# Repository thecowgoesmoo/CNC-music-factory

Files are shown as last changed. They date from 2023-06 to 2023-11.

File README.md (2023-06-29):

# CNC-music-factory
This is my set of upgrades to a baseline 3018 CNC to support machining of wood for guitar necks, organ pipes, and other noisy bits.

The resulting machine has nearly 5x the cutting volume (300mm x 775mm x 50mm instead of the stock volume of 300mm x 180mm x 45mm) and 10 times the power (The spindle has been upgraded from the stock 75W one to a 750W Bosch Colt router).

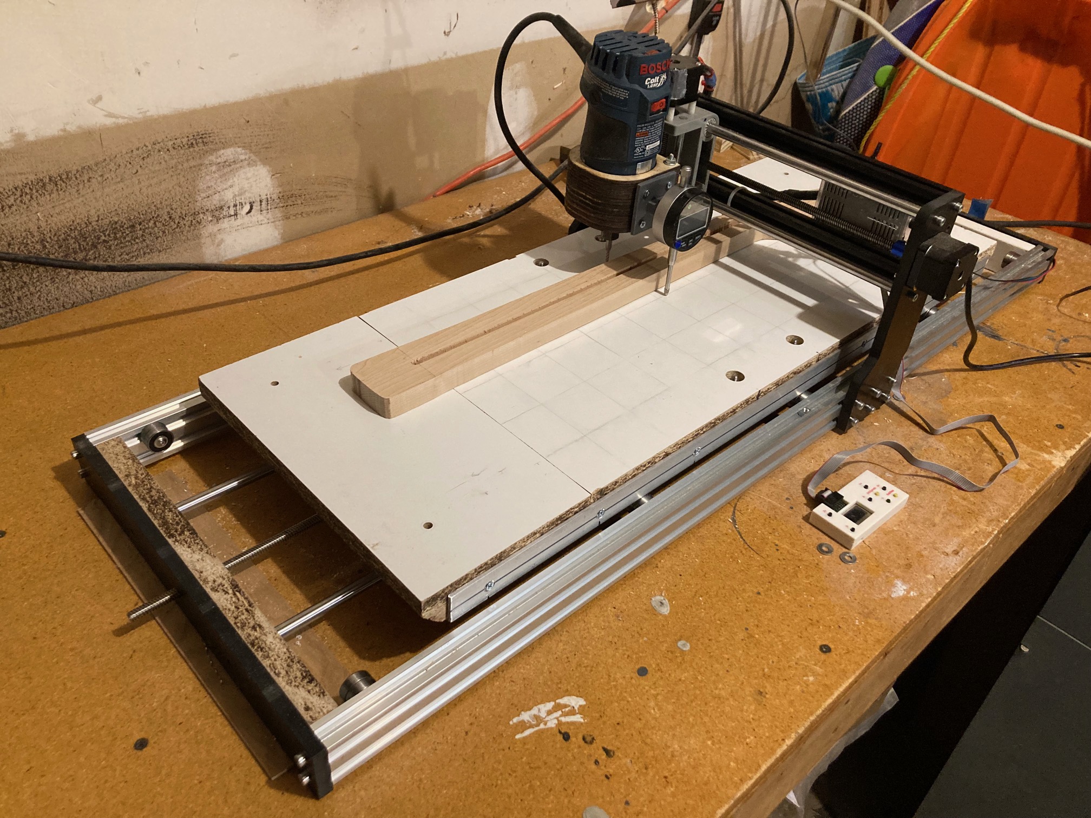
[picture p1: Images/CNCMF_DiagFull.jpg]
Overview image


## Overview
Playing music and making/modifying musical instruments has been a lifelong hobby of mine.  Electronic instruments have long been more accessible to DIY hobbyists given the increasing availability of custom printed circuit boards and the relatively low cost of basic electronic assembly tools.  3D printing and affordable hobbyist CNC machines have made construction of custom acoustic and electromechanical instruments more accessible than ever before.  

3D printing has been exciting, but available materials are not ideal for some acoustic applications (relatively high density and low stiffness compared to wood, for instance).  Laser cutting is a strong complementary technology, and K40 lasers have also achieved a <$500 USD price point, but these are largely limited to 2 dimensional cuts.  

A Genmitsu 3018 CNC has opened up new materials and geometries to me and had an initial price that was within my reach (<$200 USD).  The CAD and CAM learning curves proved considerably steeper than the SW tools for 3D printing, where large databases of free designs are readily available online and slicing SW is now relatively mature, general, and user-friendly.  And as I learned to use the 3018, its actual power, geometry, and accuracy proved to be quite constraining.  In particular, I was interested in being able to machine guitar necks from wood in less than a day of machining and without workpiece tiling.  As with lasers, there is a considerable price jump from the entry-level machines (~$200USD) to mid-level hobby machines (>$1000USD). 

My solution has been incremental upgrades, first to improve accuracy, then power, then machining volume.  The resulting machine appears to fill a capability and price point gap in the current commercial offerings (~$250USD beyond the baseline 3018 cost for 10x spindle power and a 1 meter y axis), so I've decided to share my set of upgrades for others to use if they please.  

## Assembly
1. Start with assembled and tested Genmitsu 3018 CNC
- a. Assuming Candle for pushing g code
- b. Assuming Fusion 360 for CAM
2. Build waste board
- a. Screw 1"x2" lumber to sides of melamine cut to dimensions
- b. Drill and countersink for mounting to aluminum plate
- c. Drill and mount aluminum side rails
- d. Bevel ends
3. Install lengthened Y axis:
- a. Remove existing Y axis v rail, linear bearing rails, and lead screw
- b. Install longer Y axis v rail, linear bearing rails (on plywood ends), and lead screw
- c. Mount extended waste board
- d. Install extension cable for stepper motor
4. Build new spindle carriage
- a. Cut profiles from plywood with laser
- b. Print assembly guides
- c. Glue, stack, and bolt with guides in place
- d. After drying, install antibacklash nut and linear bearings
- e. Mount new carriage on lead screw and linear rails and couple to stepper motor
5. Final bits
- a. Install 608 rollers under bed
- b. Print and install guide rollers for side/top
- c. Install carriage and check full range of travel for all axes
- d. Print and install meter mount
- e. Update GRBL setting for Y axis scaling
- f. Check bed leveling with meter
- g. Attach pen and draw shapes CW and CCW to check for backlash
6. First cut
- a. Run circle diamond square test

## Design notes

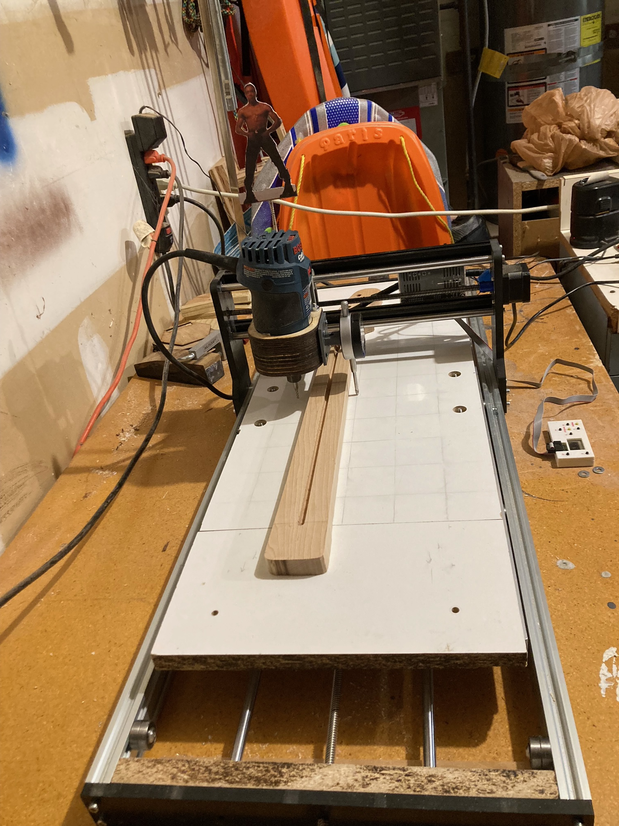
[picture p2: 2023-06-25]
Images/CNCMF_fromY.jpeg

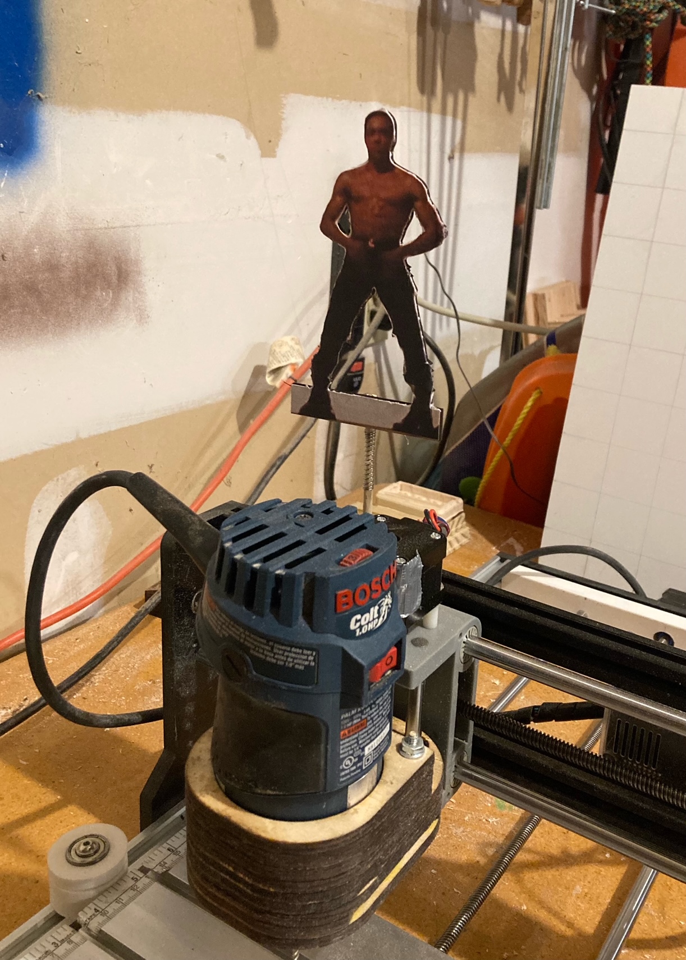
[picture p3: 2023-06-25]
Images/LetTheRhythmMoveYou.jpeg

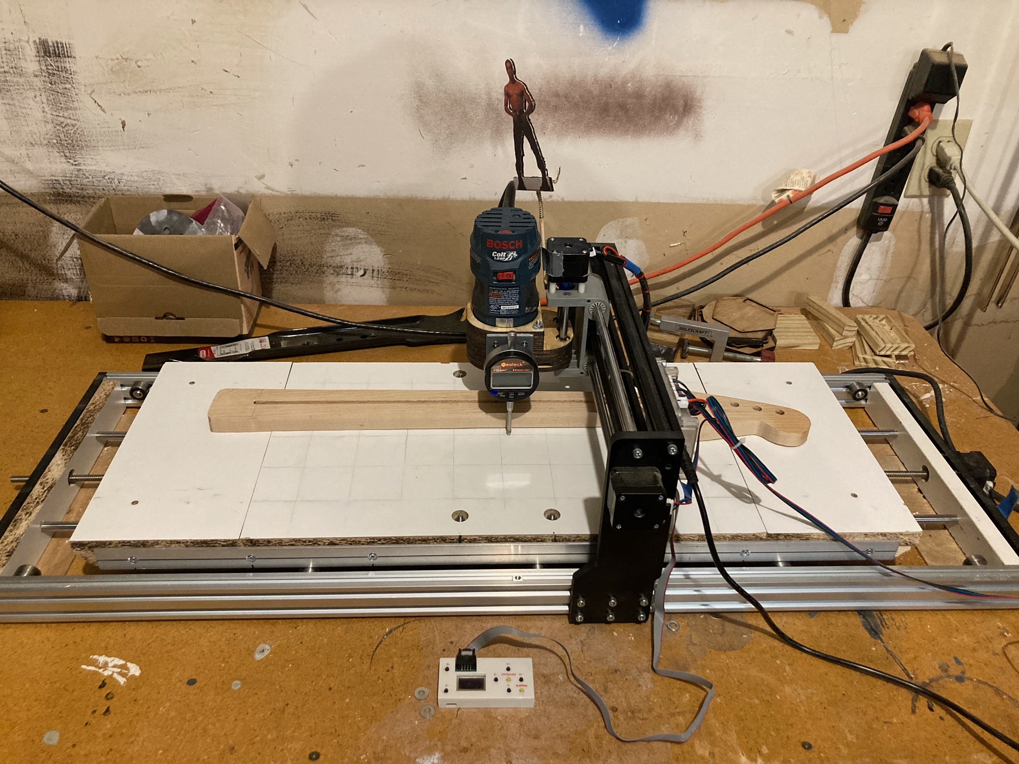
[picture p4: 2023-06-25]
Images/CNCMF_fromX.jpeg

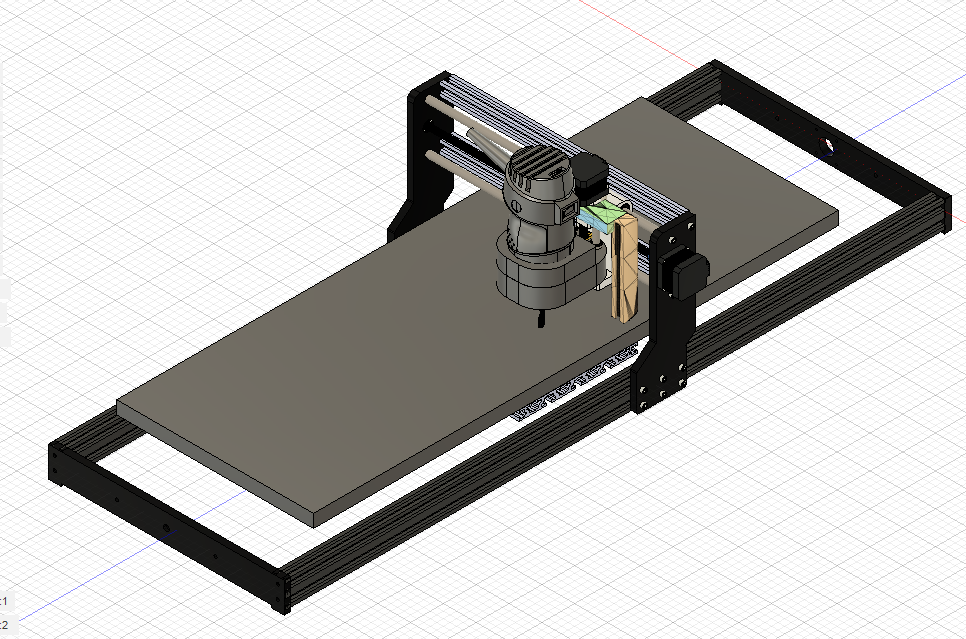
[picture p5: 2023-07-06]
Images/CAD render of full machine.PNG

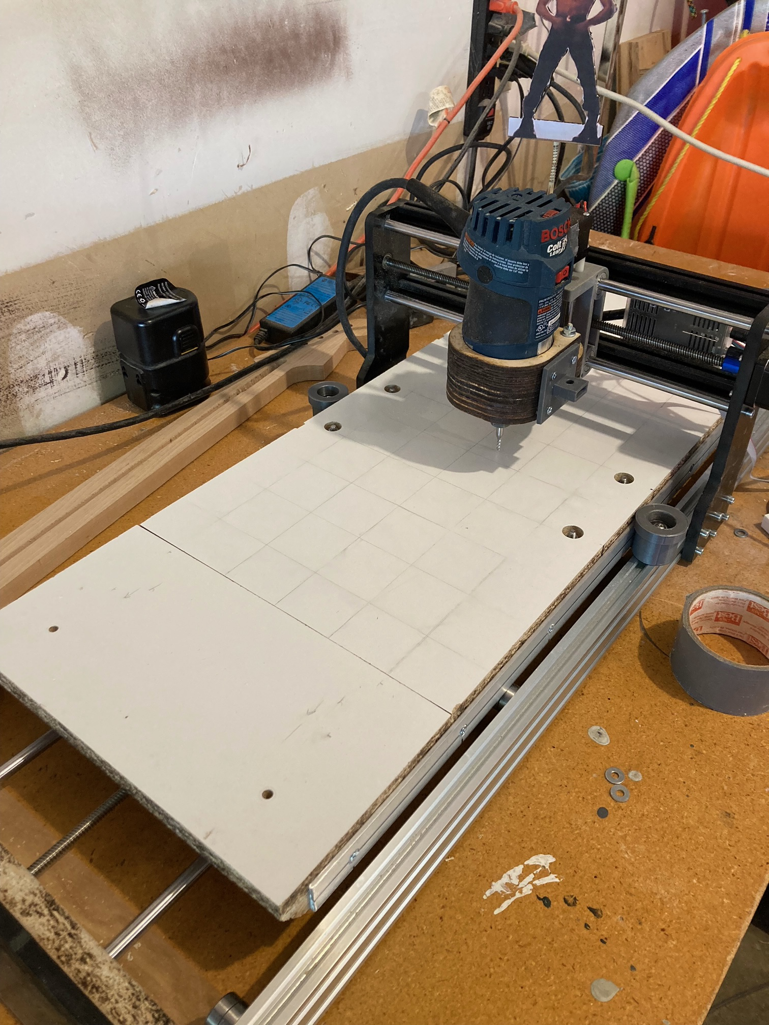
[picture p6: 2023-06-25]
Images/CNCMF_fromDiag.jpeg

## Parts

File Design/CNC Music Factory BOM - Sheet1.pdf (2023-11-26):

Part | Quantity | Price | Line total price | Link
Genmitsu 3018 CNC | 1 | $179.00 | $179.00 | https://www.amazon.com/Genmitsu-3018-PRO-Control-Engraving-300x180x45mm/dp/B07P6K9BL3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
Bosch Colt Router | 1 | $81.70 | $81.70 | https://www.amazon.com/Bosch-1-Horsepower-Electronic-Variable-Speed-PR20EVS/dp/B01M0J08MF
1040mm T8 lead screw | 1 | $33.99 | $33.99 | https://openbuildspartstore.com/8mm-metric-acme-lead-screw/
2040 v-slot rails | 2 | $13.99 | $27.98 | https://openbuildspartstore.com/v-slot-20x40-linear-rail/
Linear rail rod | 2 | $22.49 | $44.98 | https://www.amazon.com/ReliaBot-1000mm-inches-Hardened-Tolerance/dp/B09RVSH2VR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
Drylin linear rail bearings, LM10UU 10 mm (set of 4) | 1 | $9.69 | $9.69 | https://www.amazon.com/Solid-Polymer-LM10UU-Bearing-shaft/dp/B075N1KH11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
Drylin linear rail bearings, LM8UU 8 mm (set of 10) | 1 | $11.72 | $11.72 | https://www.amazon.com/Igus-RJ4JP-01-08-Printer-Bearing-replacement/dp/B07B3PZ7JH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
Anti-backlash nut (set of 2) | 1 | $9.99 | $9.99 | https://www.amazon.com/dp/B092YN16SD?psc=1&ref=ppx_yo2ov_dt_b_product_details
Plywood for spindle carriage | 1 | $7.99 | $7.99 | https://www.homedepot.com/p/Columbia-Forest-Products-1-4-in-x-2-ft-x-2-ft-PureBond-Red-Oak-Plywood-Project-Panel-Free-Custom-Cut-Available-2830/204771223
608 bearings (set of 100) | 1 | $18.79 | $18.79 | https://www.amazon.com/dp/B073ST742Z?psc=1&ref=ppx_yo2ov_dt_b_product_details
v-slot t nuts (set of 40) | 1 | $6.55 | $6.55 | https://www.amazon.com/dp/B08D76VK5Q?psc=1&ref=ppx_yo2ov_dt_b_product_details
M5 bolts assortment (50 pcs) | 1 | $9.89 | $9.89 | https://www.amazon.com/dp/B07GVPWYP8?psc=1&ref=ppx_yo2ov_dt_b_product_details
Stepper motor extension cables | 1 | $13.99 | $13.99 | https://www.amazon.com/dp/B07SLPLPL2?psc=1&ref=ppx_yo2ov_dt_b_product_details
Genmitsu limit switch set | 1 | $11.99 | $11.99 | https://www.amazon.com/Genmitsu-Micro-Switches-3018-PROVer-3018-MX3/dp/B08P1D6WTR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
T-nut inserts for wasteboard (set of 50) | 1 | $7.99 | $7.99 | https://www.amazon.com/dp/B00XXFZ5FE?psc=1&ref=ppx_yo2ov_dt_b_product_details
5/8" Waste board | 1 | $7.98 | $7.98 | https://www.homedepot.com/p/Rubbermaid-White-Laminated-Wood-Shelf-12-in-D-x-36-in-L-FG4E1900WHT/202753295
1" x 2" x 4' dimensional lumber | 1 | $2.99 | $2.99 | https://www.homedepot.com/p/2-in-x-2-in-x-4-ft-Pressure-Treated-Lumber-559000102020400/100035795
1/8" x 1" x 36" aluminum stock | 2 | $12 | $24.94 | https://www.homedepot.com/p/Everbilt-1-in-x-48-in-Aluminum-Flat-Bar-with-1-8-in-Thick-801927/204274000
Printed limit switch mounts | 6 | $0 | $0.00 | Thingiverse link
Modified z axis mounting rail | 1 | $0 | $0.00 | Thingiverse link
Printed y table nut fitting | 1 | $0 | $0.00 | Thingiverse link
Printed bottom bearing bushings | 4 | $0 | $0.00 | Thingiverse link
Printed side roller wheels | 6 | $0 | $0.00 | Thingiverse link
| | Total cost | $512.15

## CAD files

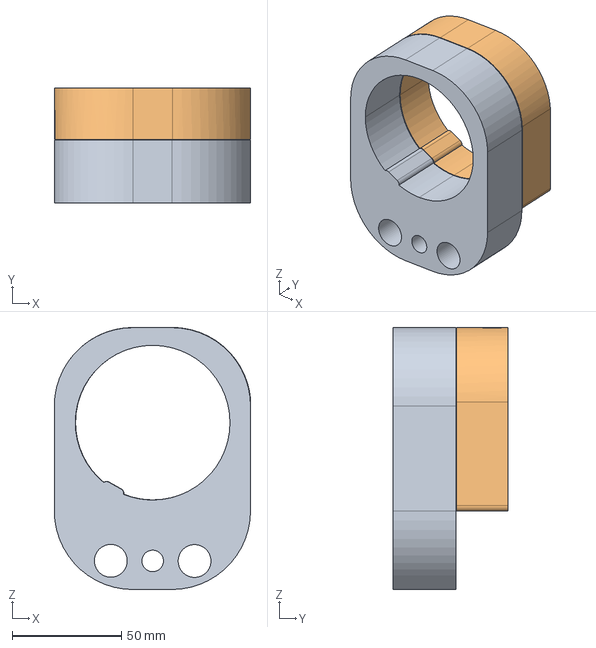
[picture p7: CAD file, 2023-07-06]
Design/Bosch Colt Spindle Carriage v3.step
89.8 x 52.6 x 119.8 mm

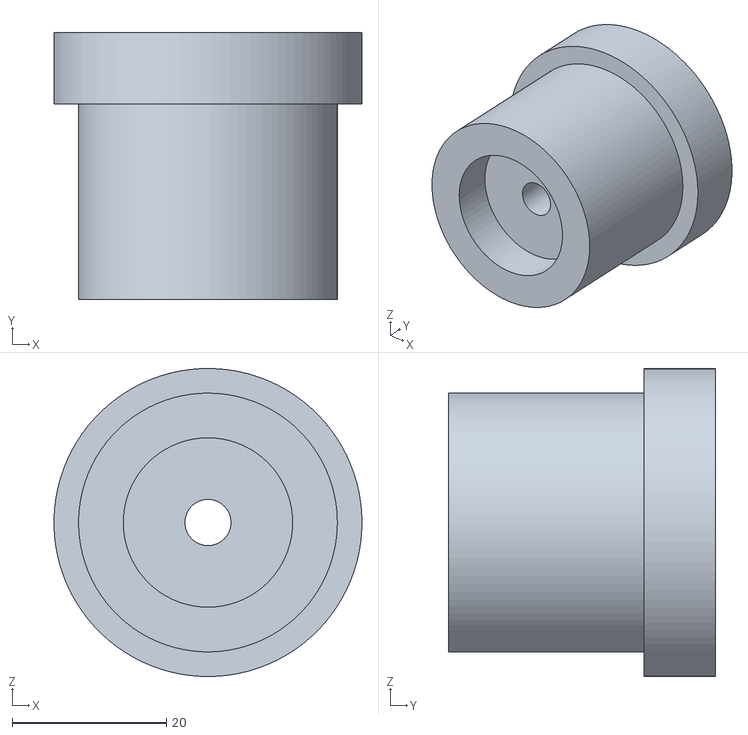
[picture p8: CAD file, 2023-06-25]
Design/CNCMF_AluminumRailSideBearing v1.stl
40.0 x 34.7 x 40.0

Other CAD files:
Design/CNCMF_zLimSwitchBracket v7.step

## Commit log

2023-06-25 Added bill of materials
    First version of the bill of materials (BOM).
    [CNC Music Factory BOM.xlsx]
2023-06-25 Added initial assembly outline to README.md
2023-06-25 Added design files carriage and guides
    .stl for 3D printing bed top & side roller guides added.
    Also added .svg files to laser cut plywood to make spindle carriage that can accommodate Bosch Colt router.
    [CNCMF_AluminumRailSideBearing v1.stl]
2023-07-06 Added some CAD files
    Adding CAD files for the spindle carriage and the modified z limit switch bracket that fits on it
    [Bosch Colt Spindle Carriage v3.step, CNCMF_zLimSwitchBracket v7.step]
2023-07-06 Added screen shot of CAD render
    The STEP file for the full machine is 29 MB, which exceeds github's 25 MB file size limit. I'll need to simplify it before uploading to the repository.
2023-11-26 Added bill of materials spreadsheet
    Bill of materials with purchase links and tallied total cost. $512 total cost, for November 2023 version of CNCMF.
